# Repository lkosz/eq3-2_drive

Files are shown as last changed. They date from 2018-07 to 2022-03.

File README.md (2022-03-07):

## Have to buy: ##

* Stepper motor: 
  * Choose with lowest coil resistance and lowest design voltage
  * tourque about 3Nm or greater
  * rather 400 steps than 200
* Display: 4-digit, 7-segment driven by TM1637
* Motor driver:
  * recommended with 1/16, 1/32 or 1/128 step resolution
  * have to provide at least design current of motor
  * have to tolerate at least 2x of motor design voltage, recommended 10x
* Arduino: Leonardo-compatible is enough, I used Blue Pro Micro
* Other:
  * 5 monostable lever switch, type: ON-OFF-ON
  * 1 rotary switch with 3 positions
  * copper cable:
    * few meters to connect driver to power supply (depends on current)
    * few meters to connect driver to stepper motor (depends on current, 0,5mm^2 should be enough in most cases)
  * 2 banana plug for power supply
  * 1 DIN-5 socket and plug
  * 1 zener diode 2-3V
  * 6 general purpose silicon diode with low reverse current
  * 6 ceramic capacitors (not necessary)
  * motor flexible clutch
  * two cases

## Schema: ##
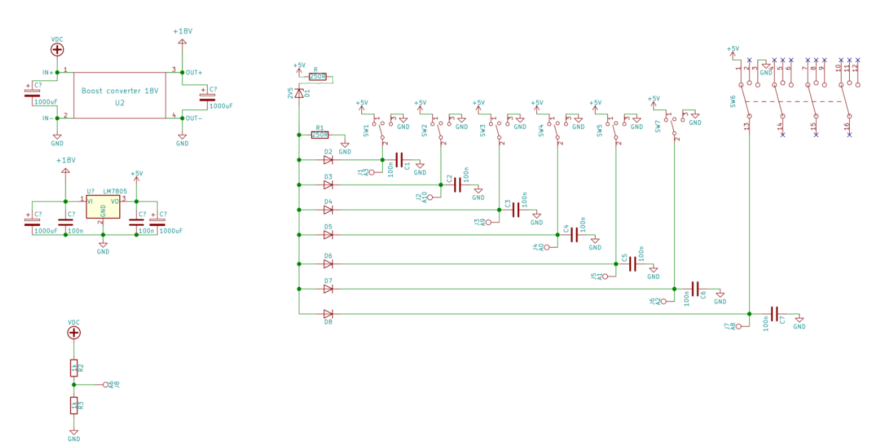
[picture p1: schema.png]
Schema


## My choices ##
* [Flexible clutch 6,35/5mm](https://static1.redcart.pl/templates/images/thumb/995/1500/1500/pl/0/templates/images/products/995/adc648671c8d53c314f9d0aac80086b8.jpg)
* [Motor SM-42BYH1684](https://botland.com.pl/silniki-krokowe/10892-silnik-krokowy-sm-42byh1684-400-krokowobr-28v-168a-048nm.html)
* [Motor driver](https://www.pololu.com/product/2970)
* [Display](https://botland.com.pl/wyswietlacze-segmentowe-led/5973-modul-4x-wyswietlacz-7-segmentowy-interfejs-cyfrowy.html)
* Blue Pro Micro
* power supply from 6V 4,5Ah AGM battery (schema in separate repo soon)

## 3D models: ##

gears are for 90 deg. transmission, holes are for molex 8981 plugs 

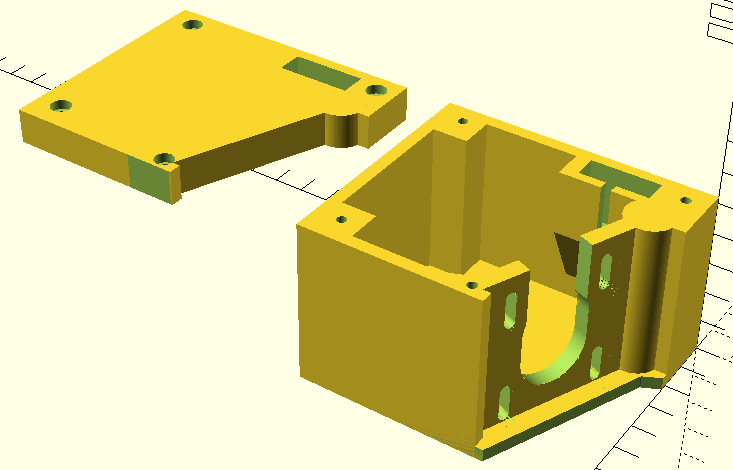
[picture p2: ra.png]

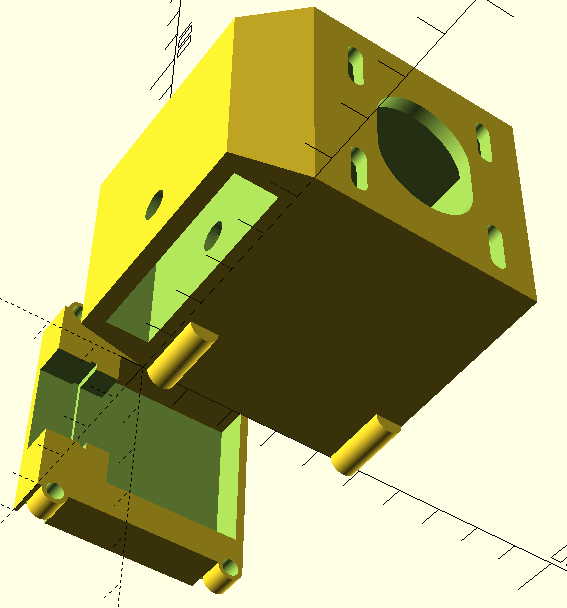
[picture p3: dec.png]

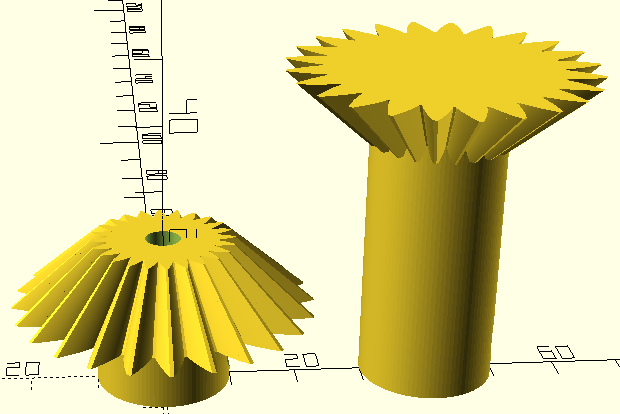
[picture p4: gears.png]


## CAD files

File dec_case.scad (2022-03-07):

$fn=200;

 module regular_polygon(n=3, d=1, h=1){
 	angles=[ for (i = [0:n-1]) i*(360/n) ];
 	coords=[ for (th=angles) [0.5*d*cos(th), 0.5*d*sin(th)] ];
  
  linear_extrude(height=h, center=true ) {polygon(coords);
  }
}


module nema17_helper(slide=8){
  
  union(){
 hull(){
 translate([0,slide/2,0]) cylinder(d=22, h=20, center=true);
  translate([0,-1*slide/2,0]) cylinder(d=22, h=20, center=true);

   }

hull(){
translate([0,slide/2,0]) translate([15.5,15.5]) cylinder(d=3.5, h=20, center=true);
translate([0,-1*slide/2,0])translate([15.5,15.5]) cylinder(d=3.5, h=20, center=true);
}
hull(){
translate([0,slide/2,0]) translate([-15.5,15.5]) cylinder(d=3.5, h=20, center=true);
translate([0,-1*slide/2,0])translate([-15.5,15.5]) cylinder(d=3.5, h=20, center=true);
}
hull(){
translate([0,slide/2,0]) translate([15.5,-15.5]) cylinder(d=3.5, h=20, center=true);
translate([0,-1*slide/2,0])translate([15.5,-15.5]) cylinder(d=3.5, h=20, center=true);
}
hull(){
translate([0,slide/2,0]) translate([-15.5,-15.5]) cylinder(d=3.5, h=20, center=true);
translate([0,-1*slide/2,0])translate([-15.5,-15.5]) cylinder(d=3.5, h=20, center=true);
}   
   }
  
}

module obudowa(){
difference(){
union(){
  
difference(){
hull(){
cube([55,49,52]);
translate([3,-15,0]) cube([48,15.5,40]);
}
translate([-3,3,3]) cube([55,44,46]);

translate([3,-14.5,0]) translate([3,3,-3]) cube([42,9,34]);

translate([55,25,25]) 
rotate([90,0,90]) nema17_helper(slide=8);
}


translate([0,4,0]) rotate([0,90,0]) cylinder(d=6, h=15);
translate([0,46,0]) rotate([0,90,0]) cylinder(d=6, h=15);
translate([0,4,52]) rotate([0,90,0]) cylinder(d=6, h=15);
translate([0,46,52]) rotate([0,90,0]) cylinder(d=6, h=15);

}

translate([-1,4,0]) rotate([0,90,0]) cylinder(d=2.6, h=15);
translate([-1,4,52]) rotate([0,90,0]) cylinder(d=2.6, h=15);
translate([-1,46,0]) rotate([0,90,0]) cylinder(d=2.6, h=15);
translate([-1,46,52]) rotate([0,90,0]) cylinder(d=2.6, h=15);

translate([27,15,10]) rotate([90,0,0]) cylinder(d=6, h=50);
translate([27,5.3-4,10]) rotate([90,0,0]) regular_polygon(n=6, d=11.6, h=4.5);
}


}
module wieko(){
difference(){
union(){
difference(){
 cube([10,49,52]);
translate([2,3,3]) cube([10,44,46]);
}

translate([0,0,2.9]) cube([10,48,5]);
translate([0,0,45]) cube([10,48,5]);
cube([10,15,48]);


translate([0,4,0]) rotate([0,90,0]) cylinder(d=6, h=10);
translate([0,46,0]) rotate([0,90,0]) cylinder(d=6, h=10);
translate([0,4,52]) rotate([0,90,0]) cylinder(d=6, h=10);
translate([0,46,52]) rotate([0,90,0]) cylinder(d=6, h=10);
}

translate([-1,4,0]) rotate([0,90,0]) cylinder(d=4, h=30);
translate([-1,4,52]) rotate([0,90,0]) cylinder(d=4, h=30);
translate([-1,46,0]) rotate([0,90,0]) cylinder(d=4, h=30);
translate([-1,46,52]) rotate([0,90,0]) cylinder(d=4, h=30);

translate([-1,4,0]) rotate([0,90,0]) cylinder(d=6.2, h=5);
translate([-1,4,52]) rotate([0,90,0]) cylinder(d=6.2, h=5);
translate([-1,46,0]) rotate([0,90,0]) cylinder(d=6.2, h=5);
translate([-1,46,52]) rotate([0,90,0]) cylinder(d=6.2, h=5);

translate([2,8,25+13.5]) rotate([0,180,270]) union(){
translate([-1,1,1]) cube([20,20,21.5]);
translate([-19,0,0]) cube([20,20,23.5]);
translate([0,0,-0.75]) cube([1.5,20,25]);
}

}





}

obudowa();
translate([-50,0,0]) wieko();

//color("red") translate([50,25,26]) rotate([0,90,0]) cylinder(d=22, h=10);

//translate([0,3,3]) color("red") cube([49,43,43]);

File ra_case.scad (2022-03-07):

$fn=100;

module rotate_around(a, v, pt) {
    translate(pt)
        rotate(a,v)
            translate(-pt)
                children();   
}
module nema17_helper(slide=8){
  
  union(){
 hull(){
 translate([0,slide/2,0]) cylinder(d=22, h=20, center=true);
  translate([0,-1*slide/2,0]) cylinder(d=22, h=20, center=true);

   }

hull(){
translate([0,slide/2,0]) translate([15.5,15.5]) cylinder(d=3.5, h=20, center=true);
translate([0,-1*slide/2,0])translate([15.5,15.5]) cylinder(d=3.5, h=20, center=true);
}
hull(){
translate([0,slide/2,0]) translate([-15.5,15.5]) cylinder(d=3.5, h=20, center=true);
translate([0,-1*slide/2,0])translate([-15.5,15.5]) cylinder(d=3.5, h=20, center=true);
}
hull(){
translate([0,slide/2,0]) translate([15.5,-15.5]) cylinder(d=3.5, h=20, center=true);
translate([0,-1*slide/2,0])translate([15.5,-15.5]) cylinder(d=3.5, h=20, center=true);
}
hull(){
translate([0,slide/2,0]) translate([-15.5,-15.5]) cylinder(d=3.5, h=20, center=true);
translate([0,-1*slide/2,0])translate([-15.5,-15.5]) cylinder(d=3.5, h=20, center=true);
}   
   }
  
}


module obudowa_cz1(){
difference(){
  union(){
    cube([85,75,4]);   
    translate([11,18,0]) cylinder(d=15, h=52);
    translate([36,76,0]) cylinder(d=15, h=52);
  };
  
  
  translate([27,15,-1]) cylinder(d=5.5,h=1000);
  translate([-11,58,-1]) cylinder(d=12.5,h=1000);
  translate([0,75,-10]) cube([100,10,100]);
  hull(){
      translate([-1,22,-1]) cylinder(d=1, h=100);
      translate([5,25,-1]) cylinder(d=1, h=100);
      translate([0,75,-1]) cylinder(d=1, h=100);
      translate([25,75,-1]) cylinder(d=1, h=100);
    }
  
};

translate([8,0,5.8]) rotate_around([0,0,-22.5], pt=[-11,58,20]) translate([20,58,20]) rotate([270,0,90]) scale([1,1,100])  difference(){
  translate([-25,-26.2,0]) cube([50,52,0.05]);
  nema17_helper();
  translate([-10,-27,-10]) cube([20,20,20]);

}

translate([28,71,0]) cube([57,4,52]);
cube([4,20,52]);
translate([81,0,0]) cube([4,74,52]);
cube([85,4,52]);


translate([0,0,0]) difference(){
  cube([15,15,15+37]);
  translate([6.5,6.5,0]) cylinder(d=3, h=100);
}
translate([70,0,0]) difference(){
  cube([15,15,15+37]);
  translate([6.5,6.5,0]) cylinder(d=3, h=100);
}
  
translate([70,60,0]) difference(){
  cube([15,15,15+37]);
  translate([6.5,6.5,0]) cylinder(d=3, h=100);
}
}

module obudowa(){
difference(){
  union(){
    obudowa_cz1();
    hull(){
    translate([15,0,32]) cube([26,14,20]);
    translate([15,0,5]) cube([26,1,10]);
    }
      };
  translate([15,3.5,33]) cube([21.5,7.6,30]);
  translate([33.5,71,33]) cylinder(d=3, h=25);
  
  //translate([6.5,0,45]) translate([-2.5, -2.5, 0]) cube([5.1,16,1.6]);
  
  //translate([76.5,0,45]) translate([-2.5, -2.5, 0]) cube([5.1,20,1.6]);
  
  //translate([76.5,56.5,45]) translate([-2.5, -2.5, 0]) cube([5.1,25,1.6]);
  
  //translate([33.5,69,45]) translate([-2.5, -2.5, 0]) cube([5.1,20,1.6]);
  translate([25,10,10]) cube([3,5,100]);

}
}

module dekiel(){
  
  difference(){
union(){
translate([15,0,32]) cube([26,14,20]);
translate([10,0,49]) cube([60,25,3]);
translate([33,0,49]) cube([40,73,3]);
translate([70,10,49]) cube([15,55,3]);
rotate([0,0,-28]) translate([-1,30,49]) cube([20,43,3]);
obudowa_cz1();
translate([8,0,5.8]) rotate_around([0,0,-22.5], pt=[-11,58,20]) translate([20,58,20]) rotate([270,0,90]) scale([1,1,100])  difference(){
  translate([-25,-26.2,0]) cube([50,52,0.05]);
}
}
translate([-1,-1,-1]) cube([100,100,42]);
translate([33.5,71,33]) cylinder(d=3, h=25);



translate([14,3.5,33]) cube([23.5,8.5,30]);

translate([14-0.75,3.5,33]) cube([25,8.5,9]);
translate([33.5,71,33]) cylinder(d=4, h=25);
translate([0,0,0]) translate([6.5,6.5,0]) cylinder(d=4, h=100);
translate([70,0,0]) translate([6.5,6.5,0]) cylinder(d=4, h=100);
translate([70,60,0]) translate([6.5,6.5,0]) cylinder(d=4, h=100);

translate([33.5,71,49]) cylinder(d=6, h=25);
translate([0,0,0]) translate([6.5,6.5,49]) cylinder(d=6.5, h=10);
translate([70,0,0]) translate([6.5,6.5,49]) cylinder(d=6.5, h=10);
translate([70,60,0]) translate([6.5,6.5,49]) cylinder(d=6.5, h=10);

}
  
  }

obudowa();
translate([100,0,0]) dekiel();

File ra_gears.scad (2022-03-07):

use <MCAD/involute_gears.scad>
use <MCAD/regular_shapes.scad>

module ra_montaz(){
$fn=100;
	gear1_teeth = 24;
	gear2_teeth = 24;
	axis_angle = 90;
	outside_circular_pitch=300;

	outside_pitch_radius1 = gear1_teeth * outside_circular_pitch / 360;
	outside_pitch_radius2 = gear2_teeth * outside_circular_pitch / 360;
	pitch_apex1=outside_pitch_radius2 * sin (axis_angle) +
		(outside_pitch_radius2 * cos (axis_angle) + outside_pitch_radius1) / tan (axis_angle);
	cone_distance = sqrt (pow (pitch_apex1, 2) + pow (outside_pitch_radius1, 2));
	pitch_apex2 = sqrt (pow (cone_distance, 2) - pow (outside_pitch_radius2, 2));
	echo ("cone_distance", cone_distance);
	pitch_angle1 = asin (outside_pitch_radius1 / cone_distance);
	pitch_angle2 = asin (outside_pitch_radius2 / cone_distance);
	echo ("pitch_angle1, pitch_angle2", pitch_angle1, pitch_angle2);
	echo ("pitch_angle1 + pitch_angle2", pitch_angle1 + pitch_angle2);

	rotate([0,180,90])
	translate ([0,0,-3])
	{
		translate([0,0,-pitch_apex1])
		bevel_gear (
			number_of_teeth=gear1_teeth,
			cone_distance=cone_distance,
			pressure_angle=30,
			outside_circular_pitch=outside_circular_pitch,
      bore_diameter=0,
      clearance = 0.5,
      face_width=15
    );

	}
difference(){
translate([0,0,-25]) cylinder(d=20, h=45);
translate([0,0,-26]) cylinder(d=6.2, h=16);
translate([0,0,-19]) rotate([0,90,0]) cylinder(d=4, h=20);
  hull(){
translate([3,0,-38]) rotate([0,90,0]) cylinder(d=8, h=3.1, $fn=6);
translate([3,0,-19]) rotate([0,90,0]) cylinder(d=8, h=3.1, $fn=6);}
translate([6,0,-19]) rotate([0,90,0]) cylinder(h=6, d1=3.5, d2=12);

}

}

module ra_silnik(){
$fn=100;
	gear1_teeth = 24;
	gear2_teeth = 24;
	axis_angle = 90;
	outside_circular_pitch=300;

	outside_pitch_radius1 = gear1_teeth * outside_circular_pitch / 360;
	outside_pitch_radius2 = gear2_teeth * outside_circular_pitch / 360;
	pitch_apex1=outside_pitch_radius2 * sin (axis_angle) +
		(outside_pitch_radius2 * cos (axis_angle) + outside_pitch_radius1) / tan (axis_angle);
	cone_distance = sqrt (pow (pitch_apex1, 2) + pow (outside_pitch_radius1, 2));
	pitch_apex2 = sqrt (pow (cone_distance, 2) - pow (outside_pitch_radius2, 2));
	echo ("cone_distance", cone_distance);
	pitch_angle1 = asin (outside_pitch_radius1 / cone_distance);
	pitch_angle2 = asin (outside_pitch_radius2 / cone_distance);
	echo ("pitch_angle1, pitch_angle2", pitch_angle1, pitch_angle2);
	echo ("pitch_angle1 + pitch_angle2", pitch_angle1 + pitch_angle2);


difference(){
  union(){
	rotate([0,0,90])
	translate ([0,0,32])
	{
		translate([0,0,-pitch_apex1])
		bevel_gear (
			number_of_teeth=gear1_teeth,
			cone_distance=cone_distance,
			pressure_angle=30,
			outside_circular_pitch=outside_circular_pitch,
      bore_diameter=0,
      clearance = 0.5,
      face_width=15
    );

	}
difference(){
translate([0,0,-0]) cylinder(d=20, h=20);
translate([0,0,6]) rotate([0,90,0]) cylinder(d=4, h=20);
  hull(){
translate([3,0,-13]) rotate([0,90,0]) cylinder(d=8, h=3.1, $fn=6);
translate([3,0,6]) rotate([0,90,0]) cylinder(d=8, h=3.1, $fn=6);}
translate([6,0,6]) rotate([0,90,0]) cylinder(h=6, d1=3.5, d2=12);
}
}

translate([0,0,-50]) cylinder(d=5.2, h=1000);

}

}

translate([40,0,25]) ra_montaz();
translate([0,0,0]) ra_silnik();

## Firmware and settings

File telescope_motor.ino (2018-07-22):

#include <SPI.h>
#include <AMIS30543.h>
#include "TM1637.h"

#define CLK 7
#define DIO 6
TM1637 tm1637(CLK,DIO);

const uint8_t amisDirPin = 2;
const uint8_t amisStepPin = 3;
const uint8_t amisSlaveSelect = 5;

AMIS30543 stepper;

/*  x = (number of steps)/(number of seconds per solar day) = (mount_ra_gear_turns * stepper_motor_steps * driver_steps_resolution)/(24*60*60)
 *  microseconds_between_steps = (int) (1/x * 10^6);
 *  picoseconds_rest = (x - (int)(x)) * 10^6
 *
 *  eg. for my mount have 1:130 gear, motor 400 steps, driver resolution 128 steps
 *  then x = 2080/27
 *  microseconds_between_steps = 12980
 *  picosecodns_rest = 769230.769230769
 */

unsigned long microseconds_between_steps = 12980;
double picoseconds_rest = 769230.769230769;
int driver_resolution = 128;
int max_miliamps = 1680;
//-----------------------------------------

bool motor_state = LOW;
bool volt_blink_state = false;
double aku_volt = 0.0;
double picoseconds_correction = 0.0;
int aku_perc = 0;
unsigned long next_butt_time = 0;
unsigned long next_disp_time = 0;
unsigned long next_step_time = 0;

//-----------------------------------------
void setup() {
  delay(3000);

  tm1637.init();
  tm1637.set(0);

  SPI.begin();
  stepper.init(amisSlaveSelect);

  digitalWrite(amisStepPin, LOW);
  pinMode(amisStepPin, OUTPUT);
  digitalWrite(amisDirPin, LOW);
  pinMode(amisDirPin, OUTPUT);
  delay(10);
  stepper.resetSettings();
  stepper.setCurrentMilliamps(max_miliamps);
  stepper.setStepMode(driver_resolution);
}

void loop() { while (1) {

  if ((unsigned long)(micros()) >= (unsigned long)(next_step_time)){
    step();
    next_step_time = next_step_time + microseconds_between_steps;
    picoseconds_correction = picoseconds_correction + picoseconds_rest;
    if (picoseconds_correction > (double)(1000000)){
      next_step_time = next_step_time + (unsigned long)(1);
      picoseconds_correction = picoseconds_correction - (double)(1000000);
    }
  }

  if (next_disp_time <= millis()){
    voltage_read();
    calc_battery_perc();
    print_voltage();
    next_disp_time = millis() + 3000;
    continue;
  }

  if (next_butt_time <= millis()){
    button_read();
    set_direction();
    next_butt_time = millis() + 50;
    continue;
  }

  delayMicroseconds((unsigned long)(microseconds_between_steps/50));

}}

void setup_motor(bool enable_motor){

  if (motor_state == LOW && enable_motor == HIGH){
    stepper.enableDriver();
    motor_state = HIGH;
    next_step_time = micros();
  }
  else if (motor_state == HIGH && enable_motor == LOW){
    motor_state = LOW;
    stepper.disableDriver();
    next_step_time = micros();
  }

}

void print_real_multiplier(int real_multiplier){
  if ( real_multiplier >= 1000 ){
    int n4 = real_multiplier%10;
    int n3 = ((real_multiplier - n4)/10)%10;
    int n2 = ((real_multiplier - n4 - n3)/100)%10;
    int n1 = ((real_multiplier - n4 - n3 - n2)/1000)%10;

    tm1637.display(0,n1);
    tm1637.display(1,n2);
    tm1637.display(2,n3);
    tm1637.display(3,n4);
  }
  else if ( real_multiplier >= 100 ){
    int n3 = real_multiplier%10;
    int n2 = ((real_multiplier - n3)/10)%10;
    int n1 = ((real_multiplier - n3 - n2)/100)%10;

    tm1637.display(0,n1);
    tm1637.display(1,n2);
    tm1637.display(2,n3);
    tm1637.display(3,16);
  }
  else if ( real_multiplier >= 10 ){
    int n2 = real_multiplier%10;
    int n1 = ((real_multiplier - n2)/10)%10;

    tm1637.display(0,n1);
    tm1637.display(1,n2);
    tm1637.display(2,16);
    tm1637.display(3,16);
  }
  else{
    int n1 = real_multiplier%10;

    tm1637.display(0,n1);
    tm1637.display(1,16);
    tm1637.display(2,16);
    tm1637.display(3,16);
  }
}

void motor_change_speed(int multiplier, bool motor_dir, int b_pin, int resolution){

  int real_multiplier = (int)(multiplier)*((int)(driver_resolution)/(int)(resolution));
  print_real_multiplier(real_multiplier);

  setup_motor(LOW);
  digitalWrite(amisDirPin, motor_dir);
  setup_motor(HIGH);

  unsigned long step_delay = (unsigned long)((unsigned long)microseconds_between_steps / (unsigned long)(multiplier)) - (unsigned long)(20);
  int state = 0;
  stepper.setStepMode(resolution);

  while (1){
    state = analogRead(b_pin);
    if ((state < 700) && (state > 50)){
      break;
    }
    step();
    delayMicroseconds(step_delay);
  }

  stepper.setStepMode(driver_resolution);
  print_voltage();
  next_step_time = micros();
  delay(20);
}

void set_direction(){
  int state = analogRead(A8);

  if (state > 990){
    setDirection(LOW);
    setup_motor(HIGH);
  }
  else if (state < 60){
    setDirection(HIGH);
    setup_motor(HIGH);
  }
  else{
    setup_motor(LOW);
  }
}

void button_read(){
  int state = 0;

  state = analogRead(A3);
  if (state > 990){ motor_change_speed(2, HIGH, A3, 128);}
  else if (state < 60){motor_change_speed(2, LOW, A3, 128);}

//---------------------------------

  state = analogRead(A10);
  if (state > 900){ motor_change_speed(8, HIGH, A10, 128);}
  else if (state < 60){motor_change_speed(8, LOW, A10, 128);}

//---------------------------------

  state = analogRead(A9);
  if (state > 900){ motor_change_speed(32, HIGH, A9, 128);}
  else if (state < 60){motor_change_speed(32, LOW, A9, 128);}

//---------------------------------

  state = analogRead(A0);
  if (state > 900){ motor_change_speed(96, HIGH, A0, 128);}
  else if (state < 60){motor_change_speed(96, LOW, A0, 128);}

//---------------------------------

  state = analogRead(A1);
  if (state > 900){ motor_change_speed(256, HIGH, A1, 64);}
  else if (state < 60){motor_change_speed(256, LOW, A1, 64);}

//---------------------------------

  state = analogRead(A2);
  if (state > 900){ motor_change_speed(512, HIGH, A2, 32);}
  else if (state < 60){motor_change_speed(512, LOW, A2, 32);}
}

void voltage_read(){
  aku_volt = (double)(analogRead(A6)) * 5.075/512 ;
}

void calc_battery_perc(){
  aku_perc = (int)((100.0 * aku_volt) - 550.0);
}

void print_voltage(){
  tm1637.display(0,1);
  tm1637.display(1,16);

  if (aku_perc > 99){
    tm1637.display(2,9);
    tm1637.display(3,9);
  }
  else if (aku_perc <= 99 && aku_perc >= 10){
    int sec_num = aku_perc%10;
    int first_num = (aku_perc - sec_num)/10;
    tm1637.display(2,first_num);
    tm1637.display(3,sec_num);
  }
  else{
    tm1637.display(2,16);
    volt_blink_state = not volt_blink_state;
    if (volt_blink_state){
      tm1637.display(3,aku_perc);
    }
    else{
      tm1637.display(3,16);
    }
  }

}

void step(){
  digitalWrite(amisStepPin, HIGH);
  delayMicroseconds(4);
  digitalWrite(amisStepPin, LOW);
  delayMicroseconds(4);
}

void setDirection(bool dir){
  delayMicroseconds(1);
  digitalWrite(amisDirPin, dir);
  delayMicroseconds(1);
}
